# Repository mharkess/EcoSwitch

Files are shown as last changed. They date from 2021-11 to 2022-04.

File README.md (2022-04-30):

# <div id="top">EcoSwitch</div>
EcoSwitch is an automated, energy-saving system for brownstone fan coil units (FCUs). It provides a BU-specific solution for maintaining comfortable dorm temperatures. Our product is simple, cost-effective, and meets the needs of BU's students and employees alike.

## Table of Contents
  <ol>
    <li>
      <a href="#engineering-addendum">Engineering Addendum</a>
      <ul>
        <li><a href="#hardware">Hardware</a></li>
        <li><a href="#software">Software</a></li>
      </ul>
    </li>
    <li>
      <a href="#software-reports">Software Reports</a>
    </li>
    <li>
      <a href="#hardware-report">Hardware Report</a>
    </li>
    <li>
      <a href="#previous-reports">Previous Reports</a>
    </li>
    <li>
      <a href="#contact-us">Contact Us</a>
    </li>
  </ol>

## Engineering Addendum

### Hardware

#### Circuit
<p align="justify">All relevant details about the connection of the circuit and its components is described in the <a href="https://github.com/mharkess/EcoSwitch/blob/main/EcoSwitch_Circuit/circuit_README.md">circuit_README </a>. It lists all the electronics specifications and steps to construct the circuit from scratch. Also, the reasons for selecting the electronics are listed there.</p>

<p align="justify">The next steps for the circuit are:</p>
- Add a LCD screen to display the temperature reading of the sensor

<p align="justify">
  
#### Attachment
<p align="justify">All relevant details about the attachment is mentioned in the <a href="https://github.com/mharkess/EcoSwitch/blob/main/EcoSwitch_attachmen/README_Hardware_Attachment.md">attachment README</a>. All the desinging concepts 3D models are listed there.</p>

<p align="justify">It is important to note that inserting a thin rubber strip in between the dial and the attachment allows the attachment to fit tighter on the switch.</p>

#### Installation and casing
<p align="justify">
  All relevant description for the device casing and installation is described in the <a href="https://github.com/mharkess/EcoSwitch/blob/main/EcoSwitch_Casing_and_install/README_Hardware_Installation.md">installation README</a>. It contains 3D models for the casing and instructions for installation.
</p>

### Software

#### Database and Server
<p align="justify">
  All relevant details about the EC2 server and MySQL database is described in the <a href="https://github.com/mharkess/EcoSwitch/blob/main/EcoSwitch_Database/README_Software_Backend.md">backend README</a>. Everything that is needed to create instances in AWS and populate those instances with the necessary files is documented there. 
</p>

The next steps for the server and the database are:
  - Add another column could be added to the database to keep track of previous temperatures and humidities to be displayed for administrators. 
  - Add error checking for API requests (for wrong data types)
  - Make SQL queries from the API to the database more secure (ex. checking the query before submitting to the database)

 <p align="justify">
  As a note, some of the PHP API calls have trouble working, even when they are set up correctly. This happens namely to tha API calls that take in arguments from the packet body and are adding/subracting rows in the database. The only work around that seemed to resolve it was to redirect the call through a API service (like AWS API Gateway), so that the request first goes to the API service, then the server (the response goes from the server to the API service).
 </p>
 
  #### EcoSwitch Device
<p align="justify">
  All relevant details about the EcoSwitch Device are described in the 
  <a href="https://github.com/mharkess/EcoSwitch/blob/main/ESP32%20Code/README_Software_ESP32.md">ESP32 README</a>. 
  Everything needed to upload the project and run it is documented in there. 
</p>

The next steps for the EcoSwitch Device are:
  - Polish UI interface for users
  - Add extra items to Administration page (Like locking device locally)

 <p align="justify">
  As a note, if the device is unable to connect to the network when it first boots, the device will reset itself on every attempt. If internet connection is lost during normal operation, then the device will continue operating normally with the exception of uploading sensor data to the database and retrieving the user's target temperature from the databae.
 </p>

#### Mobile Application
<p align="justify">
  To begin development, please follow the instructions outlined in the 
  <a href="https://github.com/mharkess/EcoSwitch/blob/main/EcoSwitchApp/README_Software_MobileApp.md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">mobile application README</a>. 
  Everything needed to initially build the project and run it is documented there. Note that some of the tools used for development were not the latest version (i.e. Expo) and updating to the latest version may cause problems with running the application.
</p>

#### Website
<p align="justify">
  All relevant details on the website's current status can be found in its corresponding <a href="https://github.com/mharkess/EcoSwitch/blob/main/EcoSwitch%20Website/README_Software_Website.md">website README</a>.
</p>

Next steps for the website:
- Authentication checking to ensure the user is logged in before being able to access the dashboard and its other linked pages
- An interactive graph that plots the average temperatures and humidity levels for each location
- Error checking for the various inputs that are allowed
  - location-related inputs: ensure the building is a valid BU brownstone location
  - room number-related inputs: ensure the room exists in the specified location
  - student email-related inputs: ensure the student email exists and is from BU
  - device registration: ensure the device does not already exist in the database
  - location locking: ensure the location is not already locked
  - location unlocking: ensure the location is not already unlocked
  - student assignment: ensure the student has not already been assigned to the specified device
  - student removal: ensure the student has not already been removed from the specified device or has never been assigned to it
- Confirmation messages for form submissions

<p align="justify">It is worth keeping in mind that the React JS version the website has been built with is newer and therefore, older articles online that provide React JS tutorials may no longer be applicable. For example, the useHistory function has been replaced with useNavigate. Additionally, for forms, it is important to prevent the page from refreshing before the API call has been completed. Using the preventDefault method achieves this. Finally, to view console outputs, use the Developer Tools Console rather than the terminal that is being used to run the server.</p>

<p align="right">(<a href="#top">back to top</a>)</p>

## Software Reports

- [Database and Server](https://github.com/mharkess/EcoSwitch/blob/main/EcoSwitch_Database/README_Software_Backend.md)
- [EcoSwitch Device](https://github.com/mharkess/EcoSwitch/blob/main/EcoSwitch_Database/README_Software_ESP32.md)
- [Mobile Application](https://github.com/mharkess/EcoSwitch/blob/main/EcoSwitchApp/README_Software_MobileApp.md)
- [Website](https://github.com/mharkess/EcoSwitch/blob/main/EcoSwitch%20Website/README_Software_Website.md)

<p align="right">(<a href="#top">back to top</a>)</p>

## Hardware Report

- [Circuit](https://github.com/mharkess/EcoSwitch/blob/main/EcoSwitch_Circuit/circuit_README.md)
- [Attachment](https://github.com/mharkess/EcoSwitch/blob/main/EcoSwitch_attachmen/README_Hardware_Attachment.md)
- [Installation and Casing](https://github.com/mharkess/EcoSwitch/blob/main/EcoSwitch_Casing_and_install/README_Hardware_Installation.md)

<p align="right">(<a href="#top">back to top</a>)</p>

## Previous Reports

- [First Semester PDRR](https://github.com/mharkess/EcoSwitch/blob/main/Project%20Reports/First%20Semester%20PDRR%20Report.pdf)
- [User Manual](https://github.com/mharkess/EcoSwitch/blob/main/Project%20Reports/User%20Manual.pdf)
- First Prototype Testing:
  - [Test Plan](https://github.com/mharkess/EcoSwitch/blob/main/Project%20Reports/Testing/First%20Prototype%20Test%20Plan.pdf)
  - [Test Report](https://github.com/mharkess/EcoSwitch/blob/main/Project%20Reports/Testing/First%20Prototype%20Test%20Report.pdf)
- Second Prototype Testing:
  - [Test Plan](https://github.com/mharkess/EcoSwitch/blob/main/Project%20Reports/Testing/Second%20Prototype%20Test%20Plan.pdf)
  - [Test Report](https://github.com/mharkess/EcoSwitch/blob/main/Project%20Reports/Testing/Second%20Prototype%20Test%20Report.pdf)
- Final Prototype Testing:
  - [Test Plan](https://github.com/mharkess/EcoSwitch/blob/main/Project%20Reports/Testing/Final%20Prototype%20Test%20Plan.pdf)
  - [Test Report](https://github.com/mharkess/EcoSwitch/blob/main/Project%20Reports/Testing/Final%20Prototype%20Test%20Report.pdf)

<p align="right">(<a href="#top">back to top</a>)</p>

## Contact Us

If there are any further questions about this project, please contact the lead developers via email.
- mharkess@bu.edu
- kevend@bu.edu
- liaophie@bu.edu
- samcu@bu.edu
- thevenin@bu.edu 

<p align="right">(<a href="#top">back to top</a>)</p>

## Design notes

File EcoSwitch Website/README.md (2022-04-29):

# <div id="top">EcoSwitch Administrator Website</div>

## Table of Contents
  <ol>
    <li>
      <a href="#about-the-project">About The Project</a>
    </li>
    <li>
      <a href="#software-module-overview">Software Module Overview</a>
      <ul>
        <li><a href="#pages">Pages</a></li>
        <li><a href="#main-functionalities">Main Functionalities</a></li>
      </ul>
    </li>
    <li>
      <a href="#dependencies-between-modules">Dependencies Between Modules</a>
    </li>
    <li>
      <a href="#development-and-build-information">Development and Build Information</a>
    </li>
    <li>
      <a href="#getting-started">Getting Started</a>
      <ul>
        <li><a href="#prerequisites-installation">Prerequisites Installation</a></li>
        <li><a href="#usage">Usage</a></li>
      </ul>
    </li>
  <li>
      <a href="#contact">Contact</a>
    </li>
  </ol>

## About The Project
<p align="justify">
  The EcoSwitch website was designed to provide housing administrators and faculty with a way to register and install new devices, as well as monitor and control currently existing ones. The original problem statement required the EcoSwitch system to be tamper-proof, so the administration website was conceptualized and developed to meet that feature.
</p>

<p align="right">(<a href="#top">back to top</a>)</p>

## Software Module Overview
<p align="justify">There are several pages that currently make up the EcoSwitch website. While some of them are simple in their functions and exist to provide information about the website and overall system, others have more significant purposes and provide access to the main features that are described in detail below.</p>

### Pages
<p align="justify">All of these pages take the form of JS functions or components that are imported and linked together in the App.js file located in the src folder of this directory.</p>

#### Home, ComponentReplace, StudentApp, and ErrorPage
<p align="justify">The home page provides an overview of our system and gives users an easy way to access the rest of the website's components, including the device registration form and housing portal sign in page.</p>
  
<p align="justify">ComponentReplace and StudentApp do not currently contain interactive content; however, they are placeholders that have been created to give users a more thorough understanding of the other features we have designed our product to contain. For example, we planned to allow the device's attachment to be swappable in case it somehow became damaged. This allows facility workers to simply replace the attachment rather than the entire device, making it a cost-effective solution. Additionally, while the mobile app is not currently available through any app store, it is an important part of our deliverables and should be accessible to our users with any future usage of our system. Finally, the error page provides users with a readable error message in case they try to access a page that does not exist. These last three pages will not be shown below due to their lack of content.</p>

<div align="center">
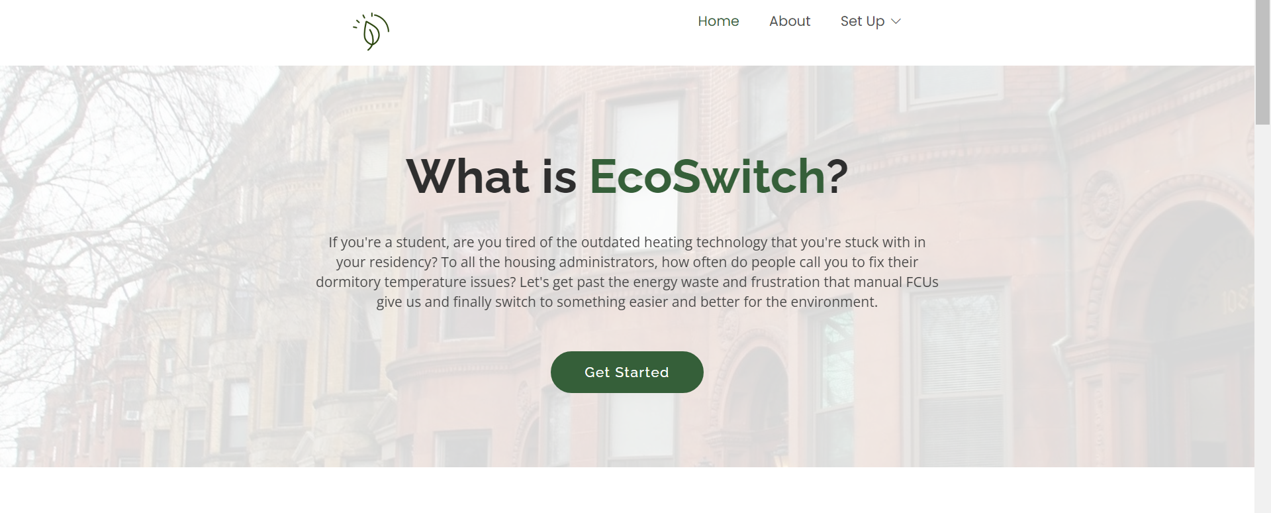
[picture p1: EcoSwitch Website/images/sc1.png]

</div>
<div align="center">
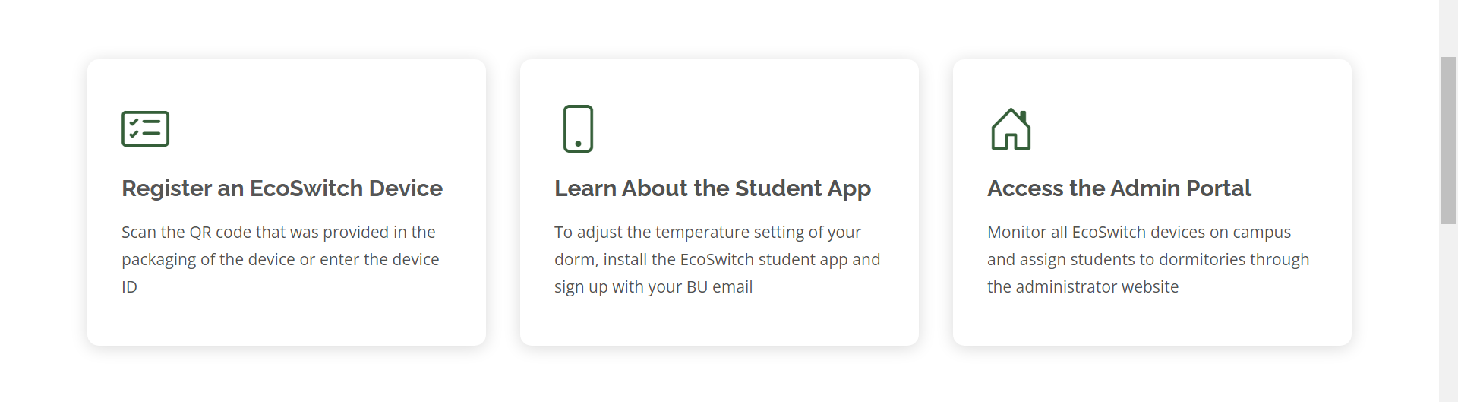
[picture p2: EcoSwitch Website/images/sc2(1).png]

</div>
<div align="center">
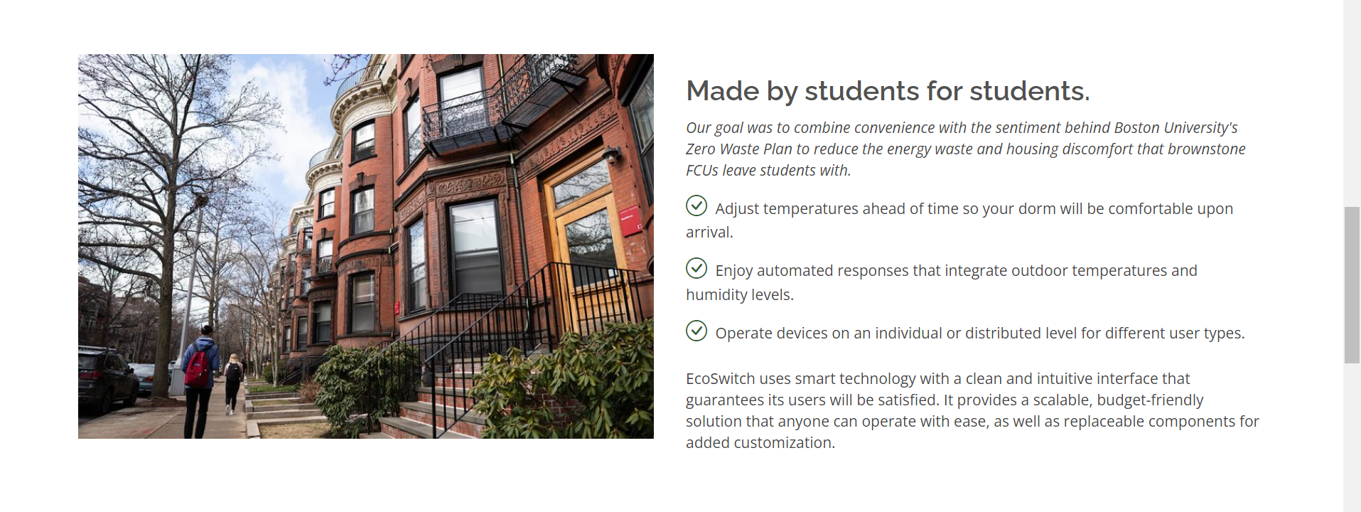
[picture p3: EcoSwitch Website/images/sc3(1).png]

</div>
<div align="center">
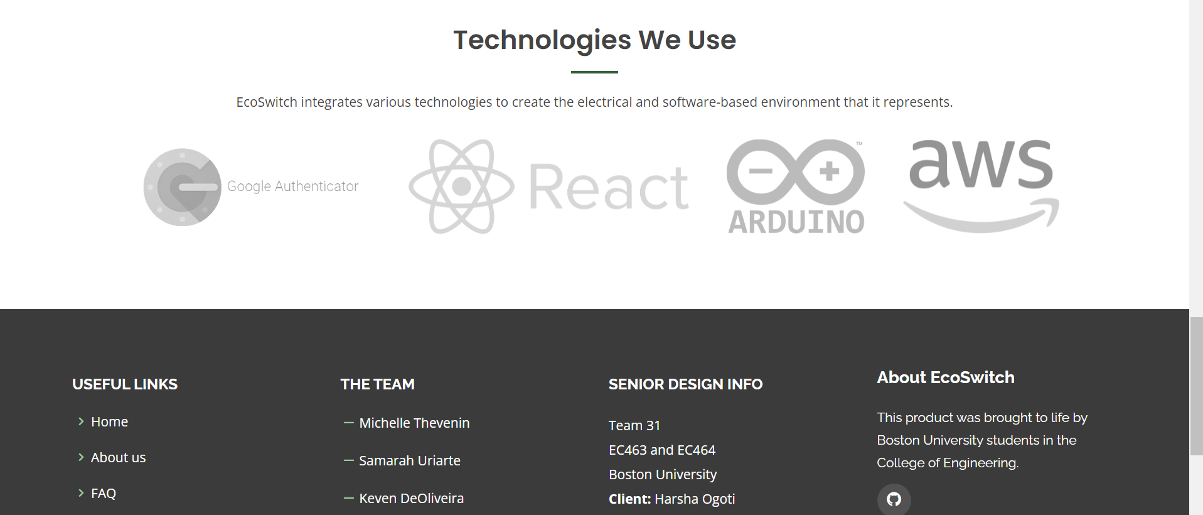
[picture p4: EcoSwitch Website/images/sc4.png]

</div>

#### Register
<p align="justify">This page is directly accessible from the website's home page and does not require users to be logged in for usage. It is important to the system's initial installation, as it allows individuals to register new EcoSwitch devices. It consists of a simple form that requests for the user to input the device ID, installation building location, installation room number. Additionally, we have designed a QR code that links to this page and would be placed within the device's packaging so users can easily scan it to set it up.</p>

<div align="center">
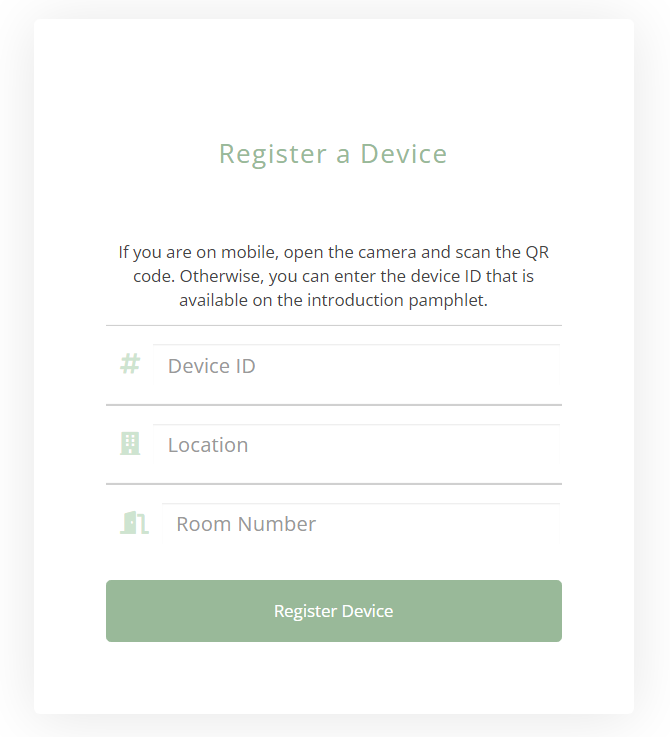
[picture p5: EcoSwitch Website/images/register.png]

</div>
</br>
<div align="center">
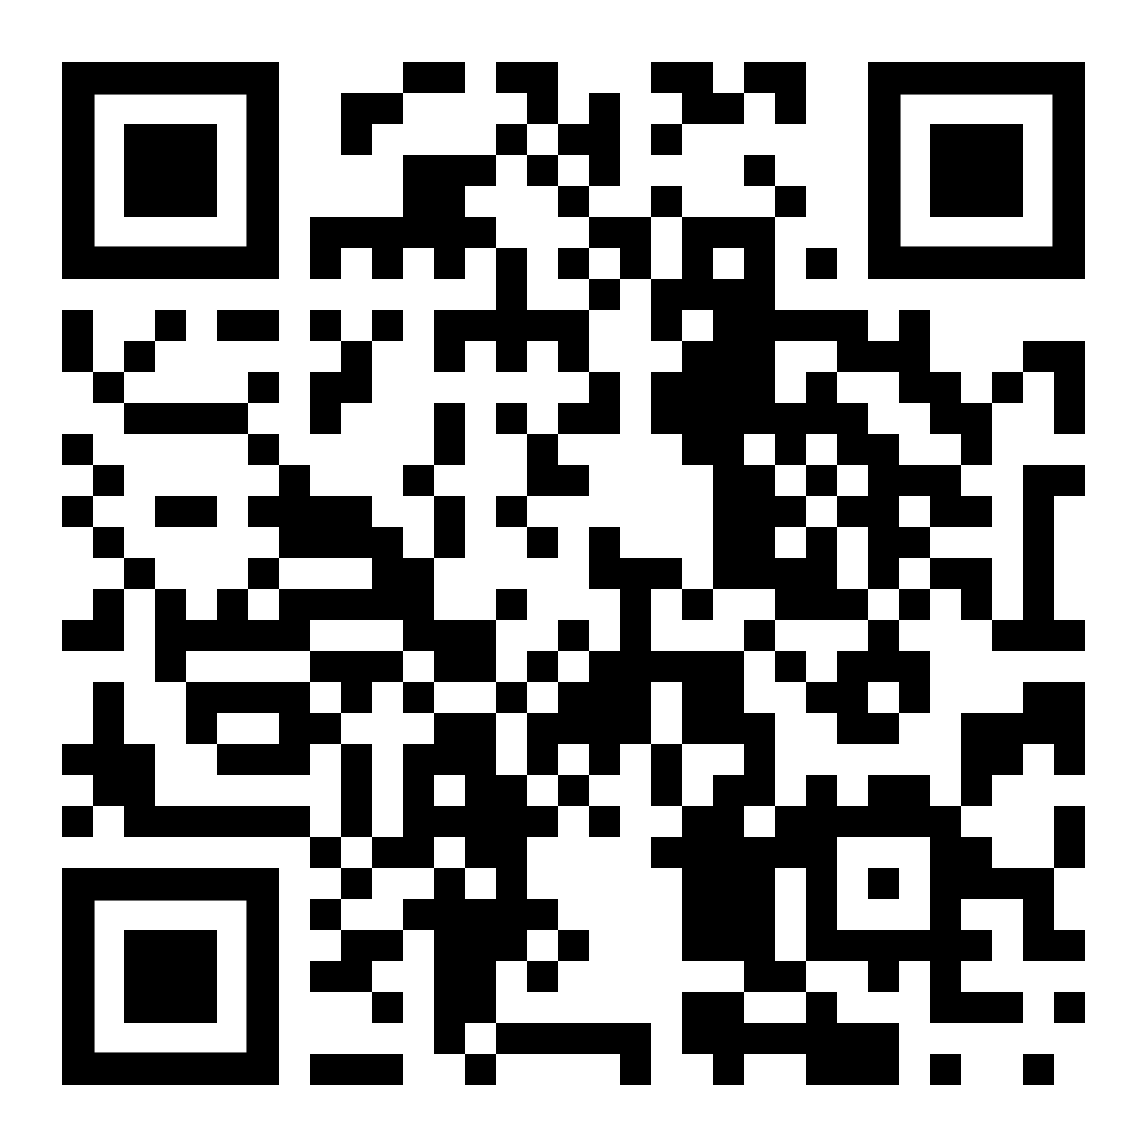
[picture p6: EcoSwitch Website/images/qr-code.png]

</div>

#### SignUp and SignIn
<p align="justify">These pages allow administrators to create an account and use it to sign in. They can also use Google as a provider and sign in with their Google account. This feature has been implemented with the JavaScript Firebase library and connects the application to a Firebase project that logs all user activity.</p>

<div align="center">
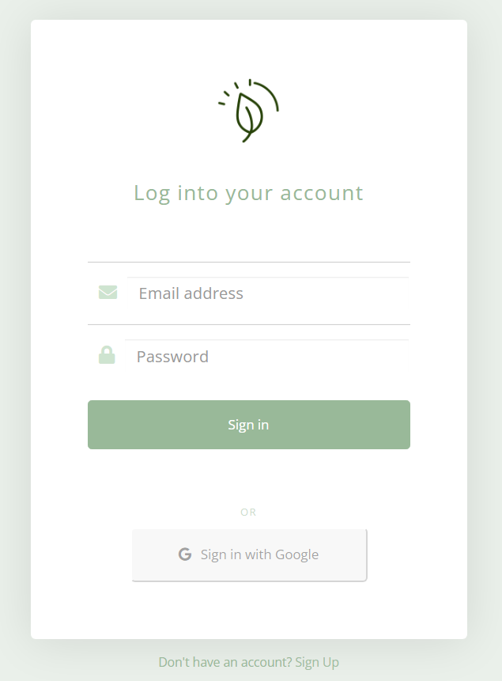
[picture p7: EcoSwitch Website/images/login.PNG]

</div>
</br>
<div align="center">
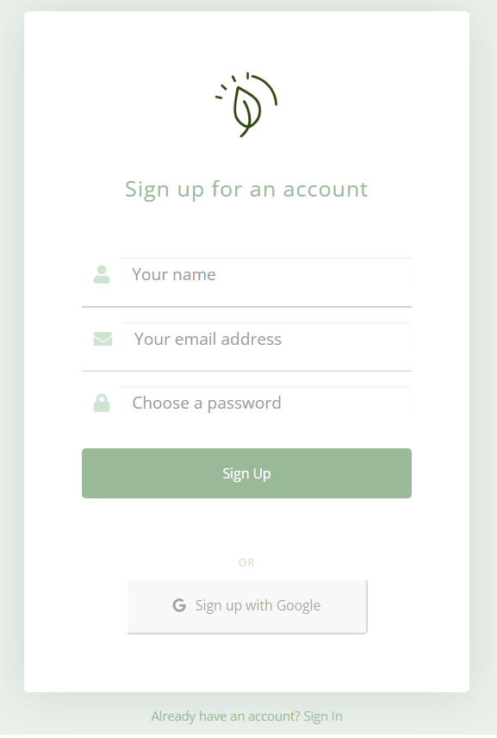
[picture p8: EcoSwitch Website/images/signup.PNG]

</div>

#### Main, DeviceAdjust, StudentAdd, and Profile
<p align="justify">The dashboard contains all the information for every EcoSwitch device that currently exists in the database. It is shown in a dynamic table that is bound to the database's entries. The empty space below was meant to hold a graph that provides a visual for the temperature and humidity levels for each building; however, this was not implemented due to a lack of time.</p>

<p align="justify">In addition to this page, there are the DeviceAdjust and StudentAdd pages that can be accessed through the sidebar. Both pages have a similar format that presents two tabs for the user to click on. Each tab brings up a separate form that does the opposite action of the other tab. For the DeviceAdjust page, there is a lock and unlock tab that allows admin to either prevent student input for a certain location and shut down all its FCUs or unlock the location and provide students with access to the devices in it again. For the StudentAdd page, one tab provides a form for registering students to a specific EcoSwitch device and the other provides a form for removing a student from a device's user list.</p>

<p align="justify">Finally, the profile page is another placeholder that has been designed to eventually display user information, such as one's name and email. Since this page does not contain any content, it has been emitted from the image set below.</p>

<div align="center">
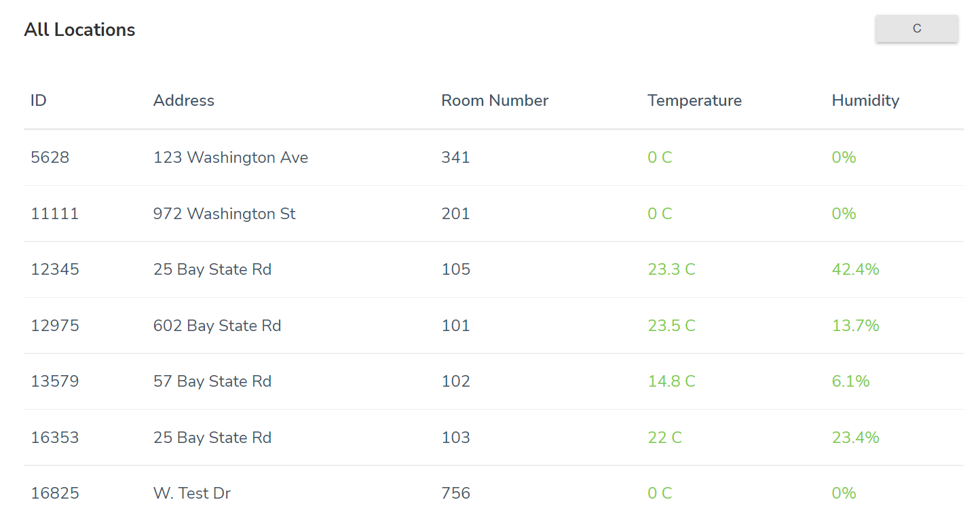
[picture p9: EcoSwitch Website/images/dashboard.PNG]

</div>
<div align="center">
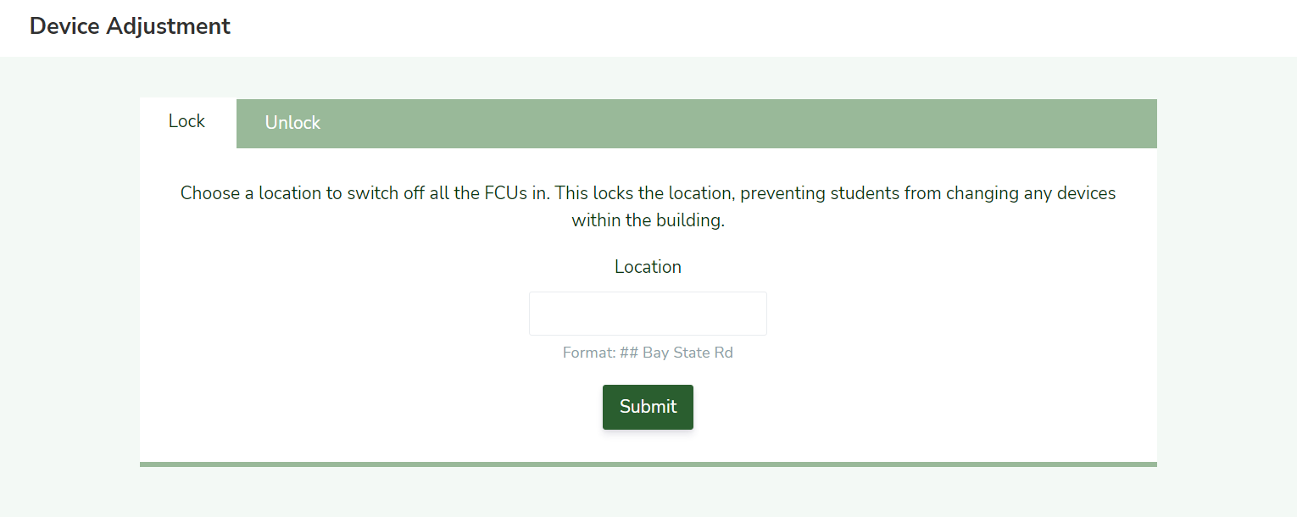
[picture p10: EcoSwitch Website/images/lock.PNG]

</div>
<div align="center">
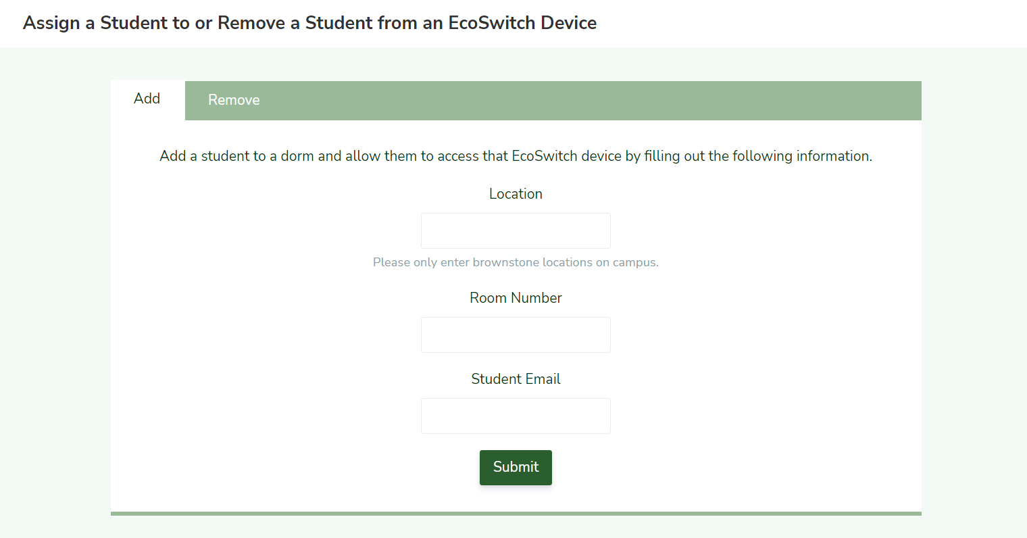
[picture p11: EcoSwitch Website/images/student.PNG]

</div>

### Main Functionalities
<p align="justify">A high-level description of all the website's main features are provided in this section, respective to the list of pages provided in the "Pages" section.</p>

#### Clean and Easy to Navigate Interface
<p align="justify">The UI and UX of the website's main pages have been designed to be user-friendly and provide content that helps them easily find their way around. The colors have also been chosen to reflect EcoSwitch's logo and general aesthetic. This is immediately evident upon the arrival of the home page, as it provides a navigation bar and large buttons that redirect users to the sign in page and device registration form.</p>

#### Device Registration
<p align="justify">As mentioned in the "Register" section, the EcoSwitch website offers the ability for users to register new EcoSwitch devices. This effectively adds them to the database and allows them to start communicating with the rest of the system. It is meant to be accessible and easy to use so the facility workers who would be setting up the devices in the dormitories would be able to do so without any difficulties. At the moment, the submission form does not have any error checking that guarantees the location and EcoSwitch ID is valid; however, this would be necessary to establish before product deployment.</p>

#### Account Creation
<p align="justify">Users are able to create an account with their email and a chosen password or through Google sign in. Upon a successful sign in request, they will be redirected to the dashboard page and their activity will be documented in the corresponding Firebase project. Currently, any individual can achieve this, though we would like there to be greater restrictions to those who can view all the EcoSwitch data and interact with the devices. However, we are unable to use Kerberos due to the security risks that would introduce. As a result, the dashboard does not require user authenitcation and the login feature has been implemented for concept development with the integration of Firebase.</p>

#### Data Querying
<p align="justify">A significant capability of the website is to communicate with the back end and its various databases through API calls. This is achieved with the JavaScript fetch function with the endpoint being chosen based on whether a GET or POST request is being made and from which database the information is being queried. API calls are used to register new devices, assign and remove students to and from EcoSwitch devices, attain all the information stored by each device, and lock and unlock specified locations.</p>

<p align="right">(<a href="#top">back to top</a>)</p>

## Dependencies Between Modules

<p align="right">(<a href="#top">back to top</a>)</p>

## Development and Build Information
All installed dependencies for the project can be found within the [package.json](https://github.com/mharkess/EcoSwitch/blob/main/EcoSwitch%20Website/package.json) and [package-lock.json](https://github.com/mharkess/EcoSwitch/blob/main/EcoSwitch%20Website/package-lock.json) files located in this directory.

This project was developed and built using the following programs and versions:

- [NodeJS v14.17.6](https://nodejs.org/en/download/)
- NPM v8.6.0

<p align="right">(<a href="#top">back to top</a>)</p>

## Getting Started

### Prerequisites Installation

Install the software mentioned above in the [Development and Build Information](#development-and-build-information) section. This varies per system and operating system. Please refer to the respective websites for further installation information.

Once the repository is cloned, navigate to this directory (.../EcoSwitch/EcoSwitch Website) and run the following code to automatically build the project and install its dependencies:

```sh
npm install
```

### Usage

For development mode, npm can be used as well.
1. In the project directory, start the session with the following command:

```sh
npm start
```
&nbsp;&nbsp;&nbsp;&nbsp;&nbsp;&nbsp;&nbsp;This will start the development server and the project can be accessed through localhost port 3000 ([http://localhost:3000](http://localhost:3000)).

**OR**

1. Access the project's pre-production build, hosted using Amplify. 
    - [Deployed Version](https://main.d3enog0k6n6e1t.amplifyapp.com/)
    - Please note that popups may be blocked, so the best way to create an account and subsequently log in is by entering your email and choosing a password through the sign-up page.

<p align="right">(<a href="#top">back to top</a>)</p>

## Contact

If there are any further questions about the application project, please contact the lead developer via email.
- samcu@bu.edu
- samarah.cu@gmail.com

<p align="right">(<a href="#top">back to top</a>)</p>

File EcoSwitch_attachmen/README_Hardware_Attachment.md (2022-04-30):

# EcoSwitch Attachment

## About the Attachemnt
  The Ecoswitch attachemnt is specifically designed to fit on top of an FCU switch located in a brownstone on Boston University’s campus. The attachment makes it possible to turn the dial using the motor. The hole at the top of the attachment is fit to the diameter of the motor shaft. Inserting rubber pieces allows for a tighter fit.</p>
Here is the 3D model:
smaller motor hole (2)
Here is the drawing:
[current attachment dimensions.pdf](https://github.com/mharkess/EcoSwitch/files/8595591/current.attachment.dimensions.pdf)

## Contact

If there are any further questions about this project, please contact the lead developer via email.
- thevenin@bu.edu 

<p align="right">(<a href="#top">back to top</a>)</p>

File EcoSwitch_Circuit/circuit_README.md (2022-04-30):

# EcoSwitch Circuit

## About the Circuit
The EcoSwitch circuit consists of an ESP32 microcontroller, a DTH22 temperature and humidity sensor, a L298N motor driver, a Nema 17 stepper motor, and a 12V battery pack with 8 AA alkaline batteries. It also includes a 5V regulator, a 10 kΩ resistor, an 100 nF ceramic capacitor, and a 1uF electrolytic capacitor.

The following is the circuit diagram:
current circuit diagram

The following is the hardware pinout of the ESP32 Pins for setup:
hardware pinout

Here is a sheet detailing our voltage measurements and power consumption:
[voltage measurement Project Team 31.xlsx](https://github.com/mharkess/EcoSwitch/files/8595606/voltage.measurement.Project.Team.31.xlsx)

Here is our Bill of Materials:
[Bill of Materials- EcoSwitch - Sheet1 (2).pdf](https://github.com/mharkess/EcoSwitch/files/8595609/Bill.of.Materials-.EcoSwitch.-.Sheet1.2.pdf)

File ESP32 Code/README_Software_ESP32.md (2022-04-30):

# EcoSwitch Device Software
## Table of Contents
  <ol>
    <li>
      <a href="#about-the-project">About The Project</a>
    </li>
    <li>
      <a href="#software-module-overview">Software Module Overview</a>
      <ul>
        <li><a href="#ecoswitch-temperature-algorithm">EcoSwitch Temperature Algorithm</a></li>
      </ul>
    </li>
    <li>
      <a href="#development-and-build-information">Development and Build Information</a>
    </li>
    <li>
      <a href="#getting-started">Getting Started</a>
      <ul>
        <li><a href="#upload-script">Upload Script</a></li>
        <li><a href="#device-setup">Device Setup</a></li>
      </ul>
    </li>
  <li>
      <a href="#contact">Contact</a>
    </li>
  </ol>

## About the Project
The EcoSwitch ESP32 code was designed to retrieve sensor data from the FCU and manage the temperature of the room via regulating the FCU temperature. This is done by running an algorithm to turn the FCU dial.  The original problem statement required the EcoSwitch device to detect temperature and humidity, and to be able to regulate the temperature based on that data. So, the ESP32 code was developed to meet that feature.

## Software Module Overview
Every aspect of the code of the ESP32 is stored on a single file. However the main part of the code that is used often is the Algorithm required to regulate the room temperature.
### EcoSwitch Temperature Algorithm
The algorithm takes the current temperature, a past temperature, the target temperature, a Boolean and the time since last running as inputs. 
The algorithm makes a slope based on the past temperature, current temperature and time. It will use this slope to calculate the predicted temperature.
Below is the formula that is used to predict the temperature:
<div align="center">

  </div>

With that predicted temperature, the algorithm will compare it to the target temperature after it compares the target temperature to the current temperature. Depending on the comparisons, the algorithm will either: increase the temperature setting by 1, decrease the temperature setting by 1 or keep the temperature setting the same.

## Dependencies Between Modules
Below is a flow chart depicting how the algorithm operates:
<div align="center">
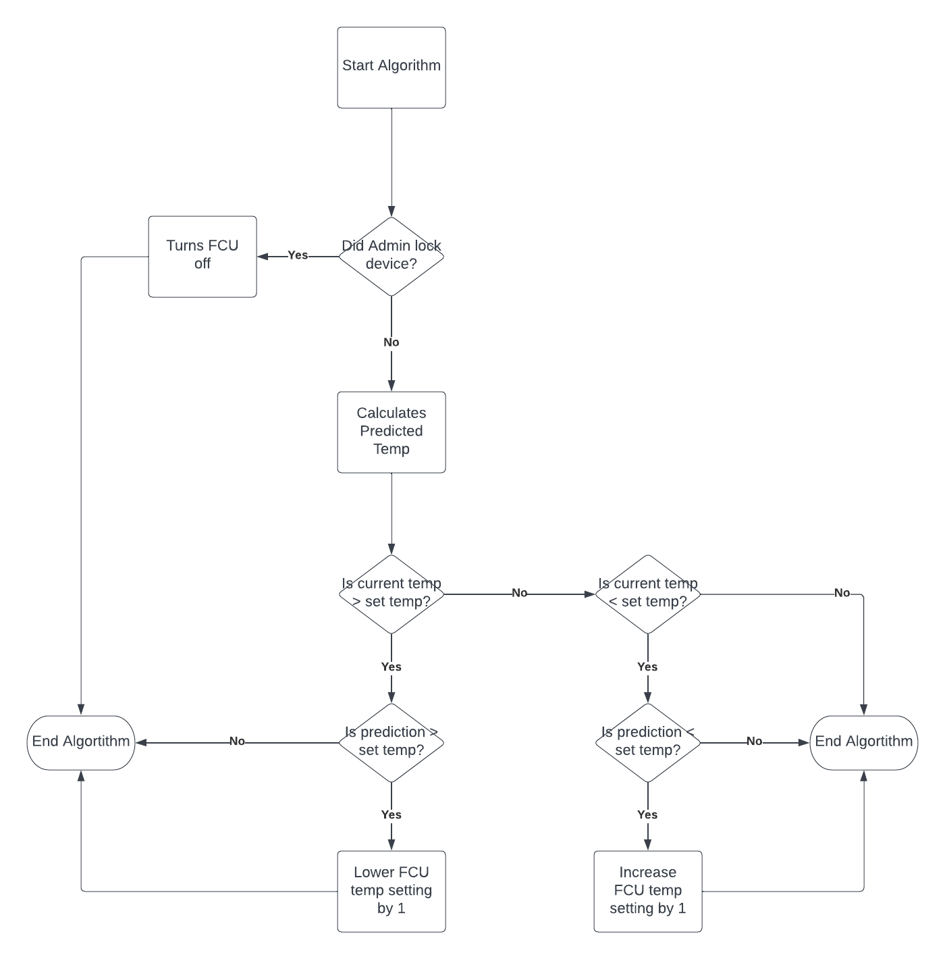
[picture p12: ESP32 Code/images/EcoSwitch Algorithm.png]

  </div>

## Development and Build Information
The program was developed with the following software:
* Arduino IDE v1.8.19

## Getting Started
### Prerequisites
You must install the ESP32 library in order to be able to program an ESP32 via Arduino IDE. Here is a tutorial that shows the exact process: [ESP32 Arduino IDE Tutorial](https://microcontrollerslab.com/install-esp32-arduino-ide/). You must also install the [AdaFruit DHT22 library](https://learn.adafruit.com/dht/using-a-dhtxx-sensor) to detect data from the DHT 22 sensor.

### Upload Script
Once the necessary libraries are installed, you can upload the ESP32 script that is provided in this repo. 
1. Navigate to `EcoSwitch/ESP32 Code/Ecoswitch_Dev/Ecoswitch_Dev.ino`. Double click on the file to open it up in Arduino IDE.
2. Once in Arduino IDE, connect the ESP32 to your computer.
3. After that upload the code to the ESP32 by clicking the "Upload" button.
<div align="center">
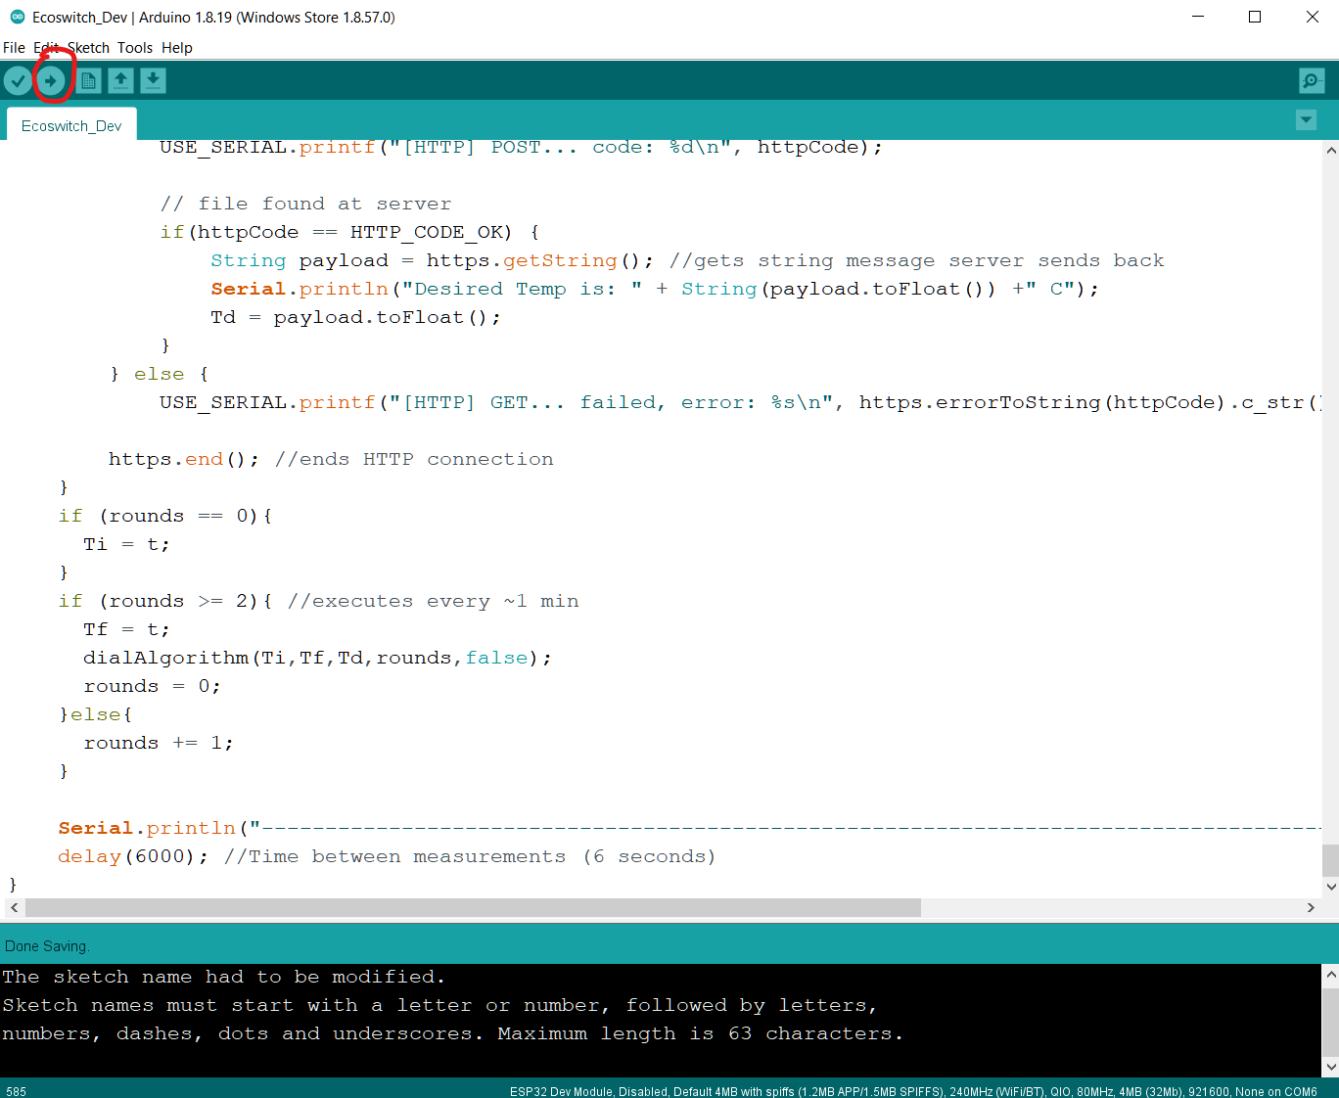
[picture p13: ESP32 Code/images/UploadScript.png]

  </div>

4. After the code has been uploaded, you can check if the code uploaded properly by opening the Serial Monitor to see if there is any output there.

### Device Setup
1. On the first boot, the device will want to know the WiFi credentials so that it can run. To do this, you must connect to the device via WiFi.
<div align="center">
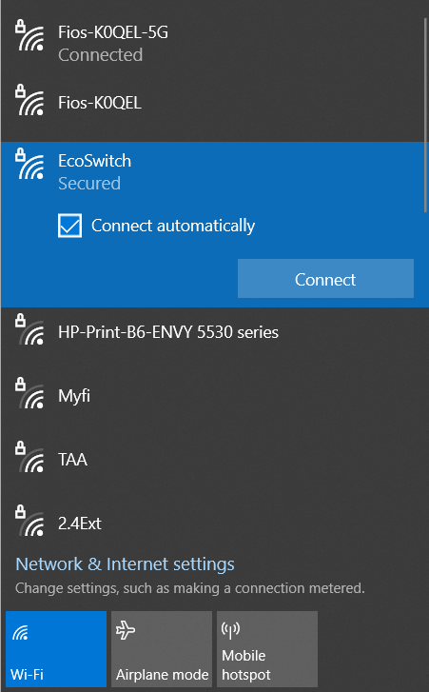
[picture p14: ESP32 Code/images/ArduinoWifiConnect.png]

  </div>

2. Once connected, navigate to `192.168.1.1` to access the HTML form to input the WiFi credentials.
<div align="center">
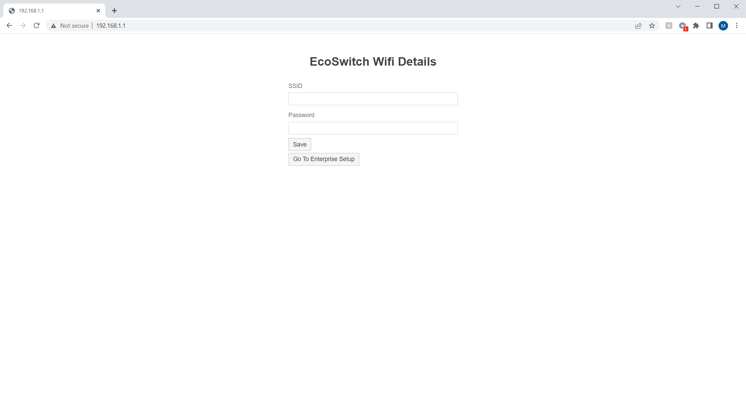
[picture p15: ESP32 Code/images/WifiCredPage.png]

  </div>

3. Once the credentials are written, click the submit button and look at the Serial Monitor to see if the device is connected to the internet.
4. If the device is connected to the internet, You will be able to see messages in the Serial Monitor regarding the Temperature, Humidity, and Current State of the device.
<div align="center">
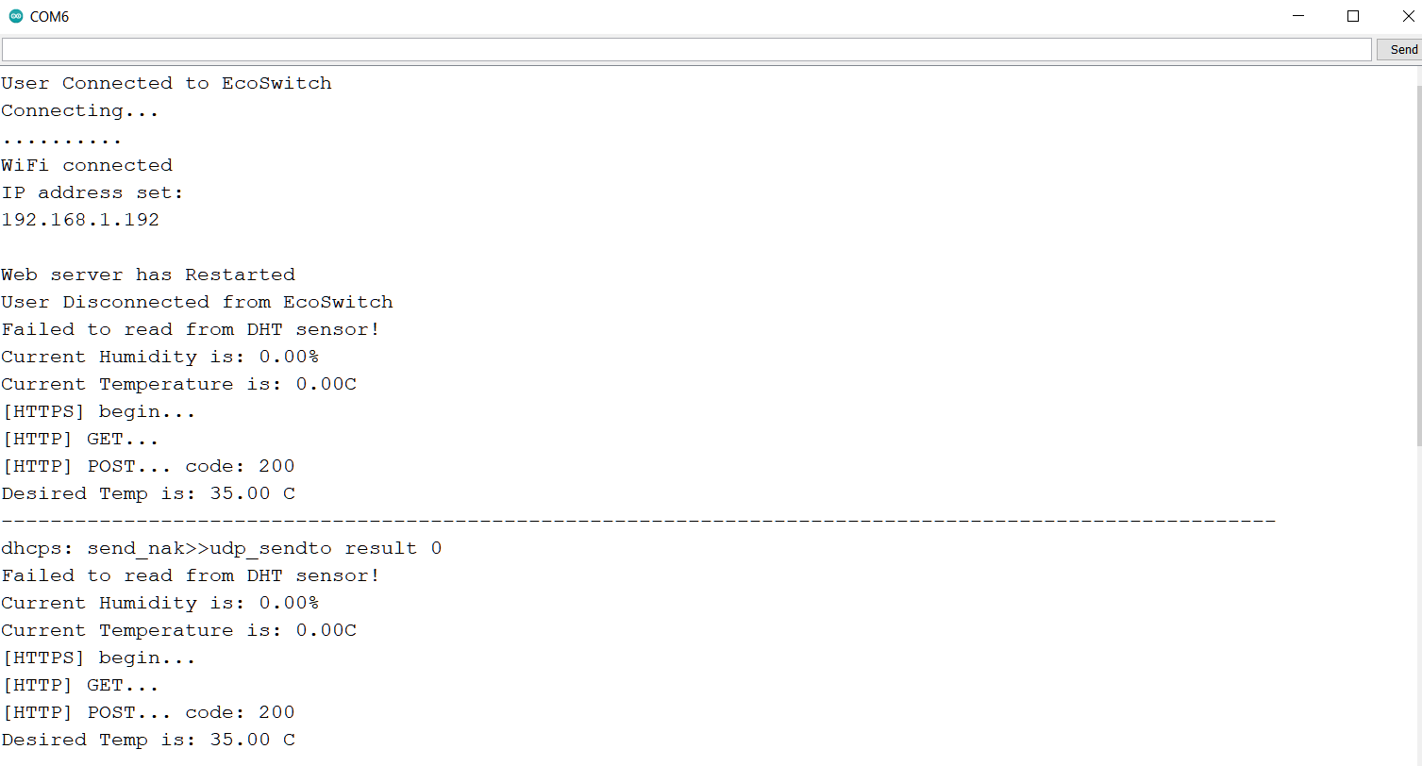
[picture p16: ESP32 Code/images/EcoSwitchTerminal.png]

  </div>

#### Potential Errors
If the device is having trouble connecting to a WiFi network, make sure that it is 2.4 GHz. If connection issues still persist after a few tries, you may want to connect to a different network (like a hotspot or an entirely different WiFi network).

## Contact
If there are any further questions about the application project, please contact the lead developer via email.
* mharkess@bu.edu

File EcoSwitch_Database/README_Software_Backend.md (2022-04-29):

# EcoSwitch Database and Server
## Table of Contents
  <ol>
    <li>
      <a href="#about-the-project">About The Project</a>
    </li>
    <li>
      <a href="#software-module-overview">Software Module Overview</a>
      <ul>
        <li><a href="#ecoswitch-api">EcoSwitch API</a></li>
      </ul>
    </li>
    <li>
      <a href="#development-and-build-information">Development and Build Information</a>
    </li>
    <li>
      <a href="#getting-started">Getting Started</a>
      <ul>
        <li><a href="#mariadb-setup-on-amazon-rds">MariaDB Setup on Amazon RDS</a></li>
        <li><a href="#apache-setup-on-amazon-ec2">Apache Setup on Amazon EC2</a></li>
        <li><a href="#amplify-hosting-setup">Amplify Hosting Setup</a></li>
      </ul>
    </li>
  <li>
      <a href="#contact">Contact</a>
    </li>
  </ol>

## About the Project
The EcoSwitch database and server was designed to store sensor data from the FCU and handle requests from users using the administrator website or the mobile application. The original problem statement required the EcoSwitch system to record temperature and humidity data, so the databases and server was developed to meet that feature.

## Software Module Overview
There are a handful of PHP files that act as the API for the EcoSwitch project. However, those files do not rely on each other in order to function. Each can be ran seperately and serve different purposes. Some update sensor data in the database and others add new records of devices to the database.

### Ecoswitch API
Below is a list of implemented API for EcoSwitch along with examples of valid calls, organized by the type of request being made. There is also a provided description of what each call is supposed to function as. Below, all of the example JSON's are assuming that you are using a JSON stringify function and a HTTP request library like fetch.  

All Requests will be received by the EC2 instance via its URL.  

So, to use the API, it would be in the format of: `URL/API`. From the API below, an example would be: `https://my-instance-public-dns-name/API/addUser.php?deviceId=<id>`

*Note: If HTTPS is giving issues when implementing the API endpoints, an alternative is using HTTP

#### GET Requests
##### /device_dataUpdate.php
  - Description: Updates temp and humidity of a particular device in the database (device is determined by their ID number)
  - Query Format:
    - `/device_dataUpdate.php?temperature=<temp>&humidity=<humidity>&deviceID=<id>` 
  - Example valid Query:
    - `https://my-instance-public-dns-name/API/device_dataUpdate.php?temperature=22.4&humidity=6.5&deviceID=12345`
##### /allUsers.php
  - Description: Retrieves table of all users in the database (table contains user's email, address and room number).
  - Query Format:
    - `/allUsers.php?deviceID=<id>`
  - Example of valid Query:
    - `https://my-instance-public-dns-name/API/allUsers.php?deviceID=12345`     
##### /allRecent.php
  - Description: Retrieves table of all devices in the database (table contains device ID, most recent temperature of their room and most recent humidity of their room).
  - Query Format:
    - `/allRecent.php?deviceID=<id>`
  - Example valid Query:
    - `https://my-instance-public-dns-name/API/allRecent?deviceID=12345`
##### /tempRequest.php
  - Description: Retrieves most recent temperature and humidity of a particular device from the database
  - Query Format:
    - `/tempRequest.php?DeviceID=<id>`
  - Example valid Query:
    - `https://my-instance-public-dns-name/API/tempRequest?DeviceID=12345` 
##### /getUser.php 
  - Description: Retrieves all information related to queried user (Email, Address, Room Number and DeviceID)
  - Query Format:
    - `/getUser.php?email=<email>`
  - Example valid Query:
    - `https://my-instance-public-dns-name/API/getUser?email=bob@bu.edu`
  - Return Value Format:
    - {"Student": "TEST@bu.edu", "Address": "101 Bay State Rd", "RoomNumber": "101", "DeviceID": "12345"}    

#### POST Requests
##### /addUser.php
  - Description: Adds users to a table relating users to the room and address that they are currently residing.
  - URL Query:
    -  `https://my-instance-public-dns-name/API/addUser`
  - Example valid JSON to send in body:
    - {"Email": "example@gmail.com", "Location": "123 Washington St", "RoomNumber": "1234"} 
##### /desiredTemp.php
  - Description: Changes the user's desired temperature of the room in the database
  - URL Query:
    -  `https://my-instance-public-dns-name/API/desiredTemp`
  - Example valid JSON to send in body:
    - {"DeviceID": "12345", "desiredTemp": "10"}
##### /changeState.php
  - Description: Locks all devices in a location to a setting of the admin's choosing
    - Note: States are defined as: -1,0,1,2,3. Any value greater than -1 will lock devices to a particular setting. State -1 allows state to be changed by student input. 
  - URL Query:
    -  `https://my-instance-public-dns-name/API/changeState.php`
  - Example valid JSON to send in body:
    - {"Location": "25 Bay State Rd", "State": "0"}
##### /removeUser.php
  - Description: Removes User from database, user will no longer to be able to control a device
  - URL Query:
    -  `https://my-instance-public-dns-name/API/removeUser.php`
  - Example valid JSON to send in body:
    - {"Location": "TEST", "Email": "TEST@bu.edu", "RoomNumber": "101"}
##### /addDevice.php
  - Description: Adds devices to a table relating devices to the room and address of the device's location.
  - URL Query:
    -  `https://my-instance-public-dns-name/API/addDevice.php`
  - Example valid JSON to send in body:
    - {"DeviceID": "46826", "Location": "972 Washington St", "RoomNumber": "10348"}  
## Dependencies Between Modules
This section provides a flowchart showing the generic movement of data from the client (via the mobile appplication or administrator website) to the database. Note that any API that is listed above can go into the second box as shown below.
<div align="center">
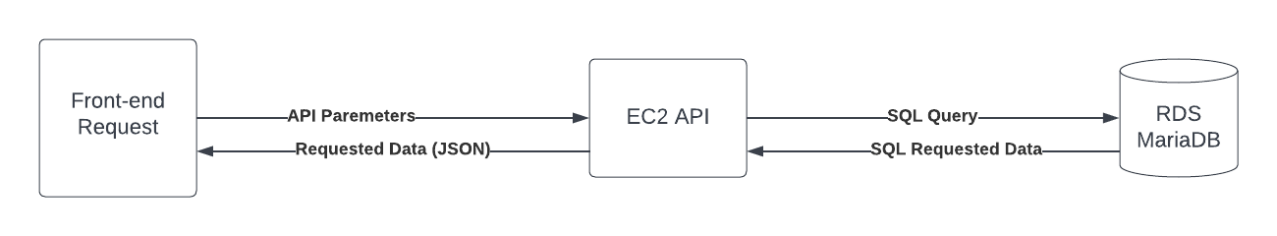
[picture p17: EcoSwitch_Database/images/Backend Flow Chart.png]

  </div>

## Development and Build Information
This project was built with the following programs, versions and hardware:
### RDS Build Information:
#### Software
* MariaDB v10.6.7
#### Hardware (Can be upgraded for better performance)
* 1 vCPU
* 1GiB RAM
* 20GiB SSD Storage
### EC2 Build Information:
#### Software
* Amazon Linux 2 Kernel v5.10 AMI 2.0.20220419.0 (with x86_64 Architecture)
* PHP v7.2
* Apache v2.4
#### Hardware (Can be upgraded for better performance)
* 1 vCPU
* 1GiB RAM
* 8 GiB SSD Storage

## Getting Started
### MariaDB Setup on Amazon RDS
1. In order to get started, you will need to have an Amazon AWS account. You can sign up for one here: [Amazon AWS](https://aws.amazon.com/free/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|PS-BI|Brand|Desktop|SU|AWS|Core|US|EN|Text&s_kwcid=AL!4422!10!71674567499740!71675011065633&s_kwcid=AL!4422!10!71674567499740!71675011065633&ef_id=d4773c0cc8251c3e64215e0735ed7a46:G:s&all-free-tier.sort-by=item.additionalFields.SortRank&all-free-tier.sort-order=asc&awsf.Free%20Tier%20Types=*all&awsf.Free%20Tier%20Categories=*all).

1. Once you have signed up for an account you will be greeted by the AWS dashboard. From here, you can follow the [RDS tutorial](https://docs.aws.amazon.com/AmazonRDS/latest/UserGuide/CHAP_GettingStarted.CreatingConnecting.MariaDB.html) to setup a MariaDB RDS instance in the AWS Documentation.

2. Once the RDS instance of the MySQL database has been created, there are two options to populate the database with schemas, tables and data. You can either SSH into the RDS instance from the command terminal or use a tool called MySQL Workbench. The continuation of the setup in this document will be using the MySQL Workbench as it provides a relatively good UI for displaying the data in the database, makes it easier to create/test SQL scripts and is a one-click connection to the cloud instance after first time setup.

The latest version of MySQL Workbench can be downloaded [here](https://dev.mysql.com/downloads/workbench/).

3. Once MySQL Workbench is opened, you can follow the [MySQL Workbench tutorial](https://dev.mysql.com/doc/workbench/en/wb-getting-started-tutorial-create-connection.html) provided by the official MySQL documentation to connect the Workbench to a remote SQL database (which in this case is the RDS instance).

4. Next, download the repo and navigate to `EcoSwitch/EcoSwitch_Database/RDS`. You will need the contents of this folder to populate the RDS instance with the appropriate schemas, tables and procedures.

5. Connect to the RDS instance via the Workbench and in the to menu, go to Edit -> Preferences -> Administration.

6. On this page, you will want to set the myssqldump.exe location to the mysqldump.exe file included in the repo (which is in `EcoSwitch/EcoSwitch_Database/RDS`).
<div align="center">
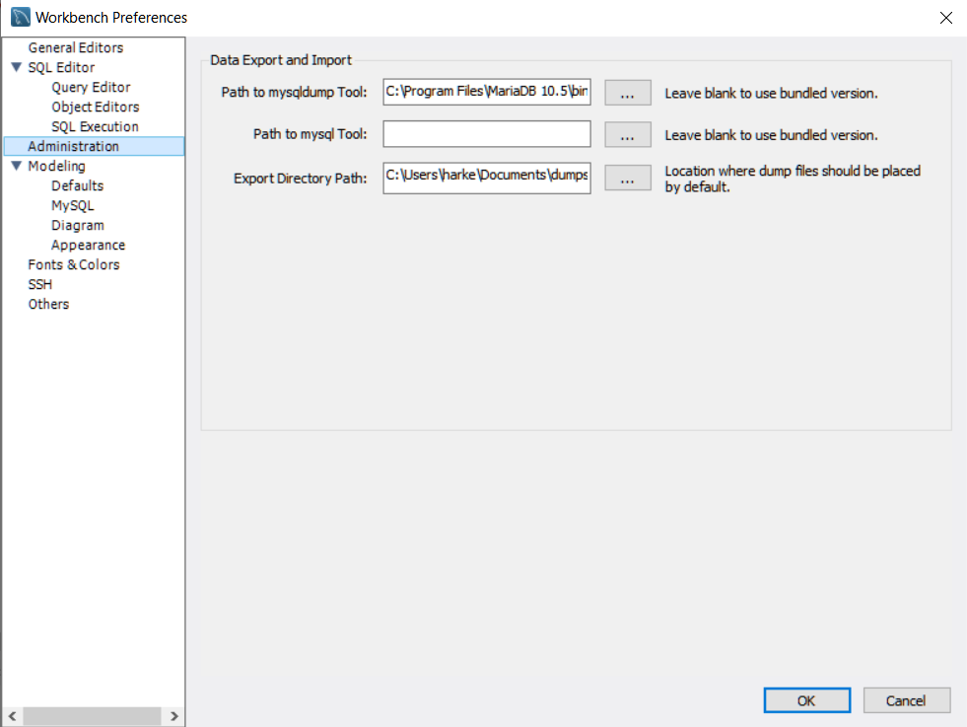
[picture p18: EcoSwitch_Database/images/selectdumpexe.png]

</div>

7. Once that is done, navigate to Server -> Data Import from the top menu. Select "Import from a Self-Contained File" and select the "EcoSwitchDB.sql" file in `EcoSwitch/EcoSwitch_Database/RDS`.
<div align="center">
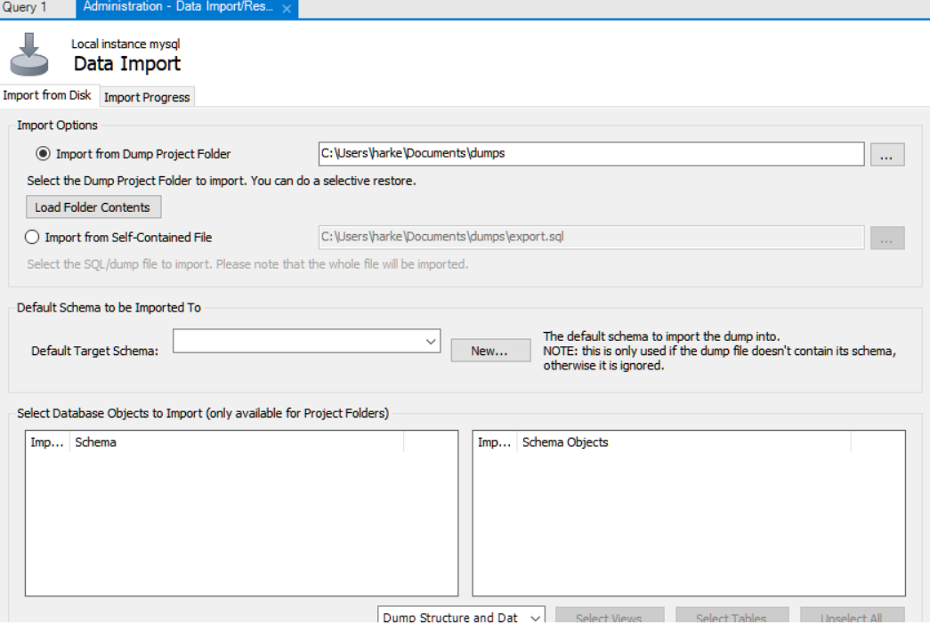
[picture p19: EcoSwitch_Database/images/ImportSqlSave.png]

</div>

8. Once the file is selected, click on the "Import Progress" tab and click the "Import" button. This should upload the schemas, test data, tables and procedures created for this project to the RDS Instance.
<div align="center">
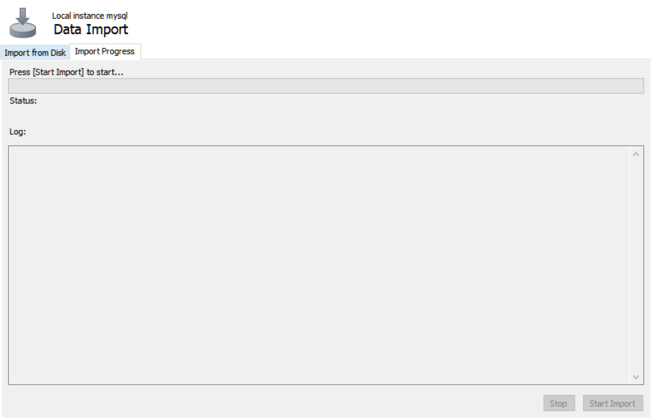
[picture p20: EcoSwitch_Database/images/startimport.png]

</div>

9. You can check the Workbench on the main page (the page that shows up after connecting to a DB) in the left side bar if all of the data is imported correctly. **NOTE:** To check the data on the left sidebar, you may need to refresh the sidebar by clicking the refresh icon at the top of the bar.
<div align="center">
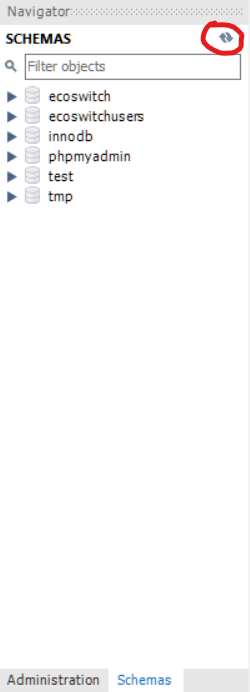
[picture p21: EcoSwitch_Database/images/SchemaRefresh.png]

</div>

### Apache Setup on Amazon EC2
To hold the API calls that this project uses, we store it on a EC2 instance running Apache to handle requests from the client.
1. Follow the setup to create an EC2 instance at this link: [EC2 Setup](https://docs.aws.amazon.com/AWSEC2/latest/UserGuide/EC2_GetStarted.html). When creating the instance, choose Amazon Linux 2 as the OS for the instance as this is the OS that this document refers to during the setup process.
2. After setting up the EC2 instance, to access the files in the instance, you will need to SSH into it. You will need at the Public IPv4 DNS to SSH, which can be found in the instances tab as well as the key-pair file created during setup (downloaded onto your machine). In order to do SSH in your terminal, you will need to run this command (you will need to replace the placeholders):
```sh
ssh -i /path/my-key-pair.pem my-instance-user-name@my-instance-public-dns-name
```

3. To configure Apache web server, PHP and MariaDB (in case you decide to not use RDS) you can follow the setup guide in this AWS documentation: [Apache Setup](https://docs.aws.amazon.com/AWSEC2/latest/UserGuide/ec2-lamp-amazon-linux-2.html).

4. To add the PHP files to the EC2 instance you can download the repository and copy the files to EC2. After the repository is downloaded you can run this command:
```sh
scp -i /path/my-key-pair.pem /path/my-php-folder ec2-user@my-instance-public-dns-name:/var/www/html
```
**NOTE:** Make sure you change the RDS URL to the URL of the instance that you have setup in the previous section for all of the PHP files before proceeding!

5. If successful, you can visit the PHP files in browser to see if they work (you can test with some of the GET API requests) with the following format: `https://my-instance-public-dns-name/API/api-call.php`

#### Potential Issues
If you are having trouble connecting to the EC2 instance, you can follow this [AWS documentation](https://docs.aws.amazon.com/AWSEC2/latest/UserGuide/AccessingInstancesLinux.html) about SSH connection to EC2.
 
### Amplify Hosting Setup
To host the admin website for this project, we decided to host it on Amplify as it could be deployed directly from the Github. To host the admin website on Amplify, navigate to the Amplify console and click on "Host Web App" in the dropdown bar in the top right of the page.
1. Click on the Github Icon on the page that loads and then you will be prompted to link your Github account to Amplify. NOTE: to deploy to Amplify in this manner, you MUST have ownership of the repo. 
2. Once your Github account is linked, you will be able to choose the repo to deploy to Amplify. Select the desired repo in the dropdown box. If you copied our repo, then you will only want to deploy a single folder in the repo. To do this, there is a selection at the bottom screen asking if you want to deploy a monorepo. Click the checkbox and then type in the path of the folder from the main file of the repo, which would be "EcoSwitch Website" (without quotations) if you are setting up the website.
3. Click next to bring you to a page showing the script that Amplify will use to compile and run the selected Web App. However, the default script must be changed to add extra libraries not included in `npm install`. Click on edit and replace the default script with the following:
```sh
version: 1
applications:
  - frontend:
      phases:
        preBuild:
          commands:
            - npm install
            - npm install firebase
            - npm install @firebase/analytics
            - npm install react-firebase-hooks
            - npm install react-chartjs-2 chart.js
        build:
          commands:
            - npm run build
      artifacts:
        baseDirectory: build
        files:
          - '**/*'
      cache:
        paths:
          - node_modules/**/*
    appRoot: EcoSwitch Website
``` 
4. After the script has been modified with the above, save it and continue clicking the next button until a "Save and Deploy" button appears. Make sure that the info that pops up on that page is correct. Once you have checked the information, click the "Save and Deploy" button and then wait between 5-8 minutes for Amplify to deploy the website.

5. Once the Web App has been deployed, Amplify will display a link to view the web app in the browser. From here you can test the website to see if it is being displayed properly and if the API calls are functioning.

#### Potential Errors
Some most of the errors that were encountered when deploying the website appeared during the build phase of the deployment. If you do get an error, you can click on the stage that failed during deployment to view the console logs. The most common errors were missing libraries (which can be added to the script above) or common coding mistakes as undeclared variables.  

## Contact
If there are any further questions about the application project, please contact the lead developer via email.
* mharkess@bu.edu

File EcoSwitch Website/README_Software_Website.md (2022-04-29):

# <div id="top">EcoSwitch Administrator Website</div>

## Table of Contents
  <ol>
    <li>
      <a href="#about-the-project">About The Project</a>
    </li>
    <li>
      <a href="#software-module-overview">Software Module Overview</a>
      <ul>
        <li><a href="#pages">Pages</a></li>
        <li><a href="#main-functionalities">Main Functionalities</a></li>
      </ul>
    </li>
    <li>
      <a href="#dependencies-between-modules">Dependencies Between Modules</a>
    </li>
    <li>
      <a href="#development-and-build-information">Development and Build Information</a>
    </li>
    <li>
      <a href="#getting-started">Getting Started</a>
      <ul>
        <li><a href="#prerequisites-installation">Prerequisites Installation</a></li>
        <li><a href="#usage">Usage</a></li>
      </ul>
    </li>
  <li>
      <a href="#contact">Contact</a>
    </li>
  </ol>

## About The Project
<p align="justify">
  The EcoSwitch website was designed to provide housing administrators and faculty with a way to register and install new devices, as well as monitor and control currently existing ones. The original problem statement required the EcoSwitch system to be tamper-proof, so the administration website was conceptualized and developed to meet that feature.
</p>

<p align="right">(<a href="#top">back to top</a>)</p>

## Software Module Overview
<p align="justify">There are several pages that currently make up the EcoSwitch website. While some of them are simple in their functions and exist to provide information about the website and overall system, others have more significant purposes and provide access to the main features that are described in detail below.</p>

### Pages
<p align="justify">All of these pages take the form of JS functions or components that are imported and linked together in the App.js file located in the src folder of this directory.</p>

#### Home, ComponentReplace, StudentApp, and ErrorPage
<p align="justify">The home page provides an overview of our system and gives users an easy way to access the rest of the website's components, including the device registration form and housing portal sign in page.</p>
  
<p align="justify">ComponentReplace and StudentApp do not currently contain interactive content; however, they are placeholders that have been created to give users a more thorough understanding of the other features we have designed our product to contain. For example, we planned to allow the device's attachment to be swappable in case it somehow became damaged. This allows facility workers to simply replace the attachment rather than the entire device, making it a cost-effective solution. Additionally, while the mobile app is not currently available through any app store, it is an important part of our deliverables and should be accessible to our users with any future usage of our system. Finally, the error page provides users with a readable error message in case they try to access a page that does not exist. These last three pages will not be shown below due to their lack of content.</p>

<div align="center">

</div>
<div align="center">

</div>
<div align="center">

</div>
<div align="center">

</div>

#### Register
<p align="justify">This page is directly accessible from the website's home page and does not require users to be logged in for usage. It is important to the system's initial installation, as it allows individuals to register new EcoSwitch devices. It consists of a simple form that requests for the user to input the device ID, installation building location, installation room number. Additionally, we have designed a QR code that links to this page and would be placed within the device's packaging so users can easily scan it to set it up.</p>

<div align="center">

</div>
</br>
<div align="center">

</div>

#### SignUp and SignIn
<p align="justify">These pages allow administrators to create an account and use it to sign in. They can also use Google as a provider and sign in with their Google account. This feature has been implemented with the JavaScript Firebase library and connects the application to a Firebase project that logs all user activity.</p>

<div align="center">

</div>
</br>
<div align="center">

</div>

#### Main, DeviceAdjust, StudentAdd, and Profile
<p align="justify">The dashboard contains all the information for every EcoSwitch device that currently exists in the database. It is shown in a dynamic table that is bound to the database's entries. The empty space below was meant to hold a graph that provides a visual for the temperature and humidity levels for each building; however, this was not implemented due to a lack of time.</p>

<p align="justify">In addition to this page, there are the DeviceAdjust and StudentAdd pages that can be accessed through the sidebar. Both pages have a similar format that presents two tabs for the user to click on. Each tab brings up a separate form that does the opposite action of the other tab. For the DeviceAdjust page, there is a lock and unlock tab that allows admin to either prevent student input for a certain location and shut down all its FCUs or unlock the location and provide students with access to the devices in it again. For the StudentAdd page, one tab provides a form for registering students to a specific EcoSwitch device and the other provides a form for removing a student from a device's user list.</p>

<p align="justify">Finally, the profile page is another placeholder that has been designed to eventually display user information, such as one's name and email. Since this page does not contain any content, it has been emitted from the image set below.</p>

<div align="center">

</div>
<div align="center">

</div>
<div align="center">

</div>

### Main Functionalities
<p align="justify">A high-level description of all the website's main features are provided in this section, respective to the list of pages provided in the "Pages" section.</p>

#### Clean and Easy to Navigate Interface
<p align="justify">The UI and UX of the website's main pages have been designed to be user-friendly and provide content that helps them easily find their way around. The colors have also been chosen to reflect EcoSwitch's logo and general aesthetic. This is immediately evident upon the arrival of the home page, as it provides a navigation bar and large buttons that redirect users to the sign in page and device registration form.</p>

#### Device Registration
<p align="justify">As mentioned in the "Register" section, the EcoSwitch website offers the ability for users to register new EcoSwitch devices. This effectively adds them to the database and allows them to start communicating with the rest of the system. It is meant to be accessible and easy to use so the facility workers who would be setting up the devices in the dormitories would be able to do so without any difficulties. At the moment, the submission form does not have any error checking that guarantees the location and EcoSwitch ID is valid; however, this would be necessary to establish before product deployment.</p>

#### Account Creation
<p align="justify">Users are able to create an account with their email and a chosen password or through Google sign in. Upon a successful sign in request, they will be redirected to the dashboard page and their activity will be documented in the corresponding Firebase project. Currently, any individual can achieve this, though we would like there to be greater restrictions to those who can view all the EcoSwitch data and interact with the devices. However, we are unable to use Kerberos due to the security risks that would introduce. As a result, the dashboard does not require user authenitcation and the login feature has been implemented for concept development with the integration of Firebase.</p>

#### Data Querying
<p align="justify">A significant capability of the website is to communicate with the back end and its various databases through API calls. This is achieved with the JavaScript fetch function with the endpoint being chosen based on whether a GET or POST request is being made and from which database the information is being queried. API calls are used to register new devices, assign and remove students to and from EcoSwitch devices, attain all the information stored by each device, and lock and unlock specified locations.</p>

<p align="right">(<a href="#top">back to top</a>)</p>

## Dependencies Between Modules
<p align="justify">This section provides a flowchart that illustrates all the dependencies and connections between the aforementioned software modules, as well as any relevant functions within them.</p>

<div align="center">
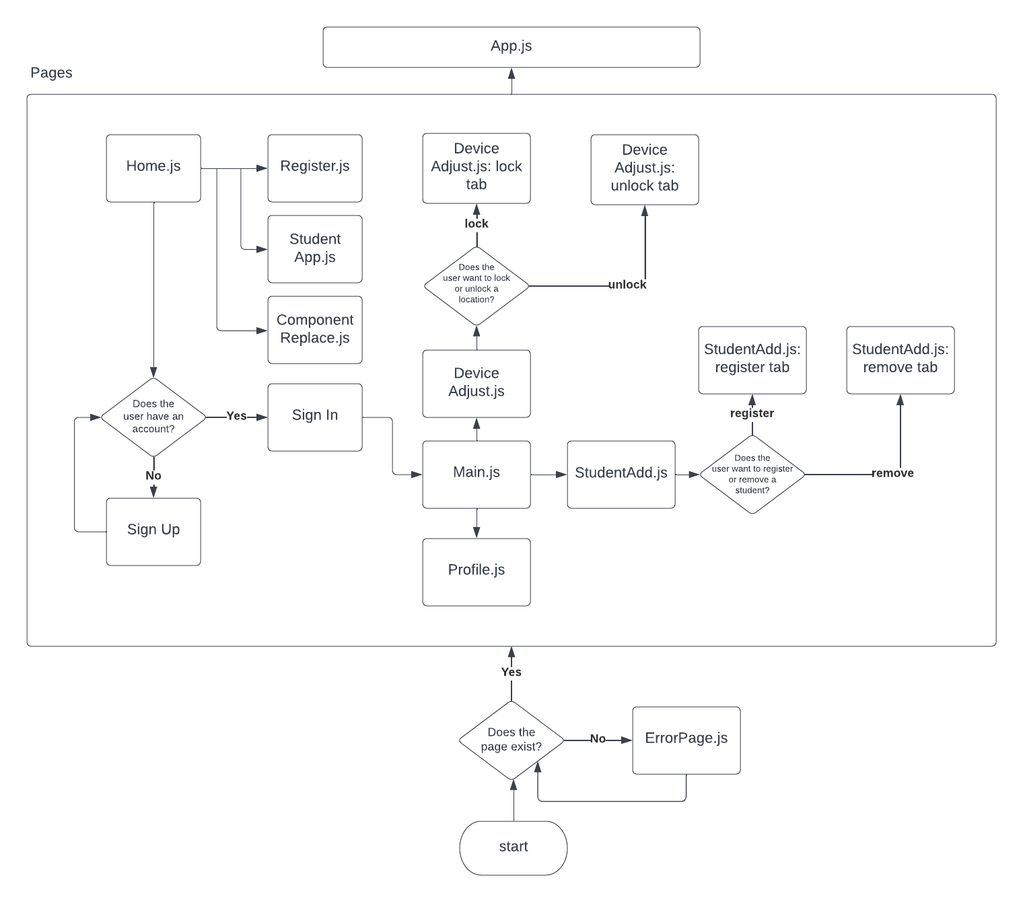
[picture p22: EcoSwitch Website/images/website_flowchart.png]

</div>

<p align="right">(<a href="#top">back to top</a>)</p>

## Development and Build Information
All installed dependencies for the project can be found within the [package.json](https://github.com/mharkess/EcoSwitch/blob/main/EcoSwitch%20Website/package.json) and [package-lock.json](https://github.com/mharkess/EcoSwitch/blob/main/EcoSwitch%20Website/package-lock.json) files located in this directory.

This project was developed and built using the following programs and versions:

- [NodeJS v14.17.6](https://nodejs.org/en/download/)
- NPM v8.6.0

<p align="right">(<a href="#top">back to top</a>)</p>

## Getting Started

### Prerequisites Installation

Install the software mentioned above in the [Development and Build Information](#development-and-build-information) section. This varies per system and operating system. Please refer to the respective websites for further installation information.

Once the repository is cloned, navigate to this directory (.../EcoSwitch/EcoSwitch Website) and run the following code to automatically build the project and install its dependencies:

```sh
npm install
```

### Usage

For development mode, npm can be used as well.
1. In the project directory, start the session with the following command:

```sh
npm start
```
&nbsp;&nbsp;&nbsp;&nbsp;&nbsp;&nbsp;&nbsp;This will start the development server and the project can be accessed through localhost port 3000 ([http://localhost:3000](http://localhost:3000)).

**OR**

1. Access the project's pre-production build, hosted using Amplify. 
    - [Deployed Version](https://main.d3enog0k6n6e1t.amplifyapp.com/)
    - Please note that popups may be blocked, so the best way to create an account and subsequently log in is by entering your email and choosing a password through the sign-up page.

<p align="right">(<a href="#top">back to top</a>)</p>

## Contact

If there are any further questions about the application project, please contact the lead developer via email.
- samcu@bu.edu
- samarah.cu@gmail.com

<p align="right">(<a href="#top">back to top</a>)</p>

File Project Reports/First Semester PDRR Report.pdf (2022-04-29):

EC463 - B OS TON UNIVER S ITY ELE C TR IC AL & COMPUTER ENGINE ER ING C AP S TONE SE NIOR DES IGN P ROJEC T

B oston University E lectrical & C omputer E ngineering C apstone S enior Design Project

# E coS witch – An Autonomous FC U Maintenance S ystem

J iawei Liao, Keven DeOliveira, Michelle Thevenin, S amarah Uriarte, and Michael Harkes s

Abstract —Manual FCUs in brownstones lead to uncomfortably warm rooms , causing occupants to either turn them off or open a window in an attempt to balance out the temperature. The former is inc onvenient and the latter results in a waste of energy. A cost -effective solution that offers multi -party accessibility is required to address this problem. To facilitate a more enjoyable housing experience and provide a centralized maintenance application to Boston University housing administrators, we propose EcoSwitch, an autonomous FCU dial mount with integrated applications which will allow both residents and managers to mon itor and adjust FCU temperatures. In addition, it will query local weather information to maintain accurate performance and store relevant information in a highly accessible database, which will allow FCU functionality to be evaluated. EcoSwitch has been o ptimized for the management of Boston University’s campus life and will establish applications with functions that are appropriate for both administrators and students.

Index Terms — Autonomous system, Design, Real-time and embedded systems , Energy efficiency and conservation

————————————————
- Jiawei Liao EE’ 22. E-mail: liaophie@bu.edu
- Keven DeOliveira CE’ 22. E-mail: kevend@bu.edu
- Michelle Thevenin EE’ 22. E-mail: thevenin@bu.edu
- Samarah Uriarte CE’ 22. E-mail: samcu@bu.edu
- Michael Harkess CE’ 22. E-mail: mharkess@bu.edu

———————— ◆ ————————

1 NEED FOR THIS PROJECT
Many brownstone apartments on Boston University’s campus still use FCUs for indoor heating in the winter. This process is not controlled by the occupants in any way. Once FCUs are turned on for the winter, they are often left on for the remainder of the season. This situation leads to an uncomfortably warm room. Occupants typically aim to solve this problem by shutting the FCU off altogether or opening a window to balance the temperature on the inside. Opening a window while an FCU is running is a direct waste of energy and valuable resources.
Building administrators want to monitor room temperatures on a weekly basis to ensure that the FCUs are working properly. At the same time, they want the FCUs to work more efficiently so that energy is not wasted. Brownstone residents want an easy way to control their room temperatures so that it stays within a desirable range. Both students and administrators want a solution that is specific to Boston University so that it is cost effective and optimized for dormitories.
Boston University has a zero waste plan that aims to eliminate all waste by 2030. The plan is to redesign systems, reuse resources, change the culture, and develop sustainable markets. With EcoSwitch, we aim to automate the FCU control system in an effort to be more conscious of Boston University’s sustainability goals. Our design supports BU’s plan by providing a solution to the waste of energy that occurs as a result of using FCUs.
EcoSwitch will address this issue by allowing students to adjust the temperature of their dormitories according to their liking. EcoSwitch will automatically adjust the FCU to the desired temperature. EcoSwitch will be designed for long-term use and will be friendly to the environment.

2 PROBLEM STATEMENT & DELIVERABLES
Our proposed system design consists of several key components that all contribute to the overall maintenance of brownstone dormitory temperature and humidity levels.

2.1 Problem Statement
By integrating autonomous technology with simple applications for customizable temperature monitoring and management, EcoSwitch solves the problems of students facing uncomfortable dorm conditions and administrators having difficulty in efficiently reducing FCU energy waste. With the goal of achieving zero waste by 2030 [1] and a more general desire to increase the quality of student life on campus, our solution has been optimized for Boston University staff and students to ensure both parties’ needs are being met.
The high-level solution that forms our system design is partitioned into two separate sets of user and application interfaces and a centralized server that will process the data received from each EcoSwitch device. This solution addresses the different functionalities students and administrators require. Options for reading in and displaying temperature and humidity levels, filtered between specific individual students’ residencies to all of Boston University’s brownstones, will be available and chosen depending on the interface. Both parties will be able to control dorm temperatures as well; however, administrators will have the

2 | EC463 - B OS TON UNIVE R S ITY ELEC TR IC AL & COMPUTER ENGINE ER ING C AP S TONE S ENIOR DES IGN
| P R OJEC T
ability to override student input to ensure energy waste is
minimized.
Both the website and mobile app clients will use sensor information and functions that control the EcoSwitch
device to achieve FCU automation and remote adjustment capabilities. To reduce computational redundancies and bandwidth requirements, the website and mobile app will connect to a single server that will have data streamed in and distributed to the appropriate user. After user responses reach the server, it will deliver back calculated temperatures after processing these inputs. Each EcoSwitch device that will be registered with a dormitory will connect to this same server; this architecture allows all EcoSwitch devices to be linked to a centralized hub for ease of data distribution. Furthermore, a database will be maintained that contains temperature and humidity levels, allowing administrators to access past information and assess FCU functionality. The EcoSwitch administrator website will also produce graphs that plot dorm conditions for up to 3 days. Local weather information will be queried for through an API and used to determine individual EcoSwitch device instructions, a feature that guarantees dorm temperatures that more accurately match user input.
The EcoSwitch device will be a compact, battery-powered apparatus that reads in temperature and humidity information and relays it to the centralized server. Comprising a temperature and humidity sensor, microcontroller, and rotary actuator, the simple and cost-effective circuit design fulfills low-cost specifications. Our hardware design also includes an inexpensive attachable component that will fasten to the actuator and can easily be swapped for a new attachment if it becomes damaged. The entire device will be subject to safety constraints which make it suitable for the environment near the FCU’s surface.
The EcoSwitch devices will be programmed to collect data every 5 minutes; thus, there is no network strain or reliance on consistent WiFi connection. Computations will be performed in the central server, iterating through each registered EcoSwitch device after taking input from either administrators or students. The calculations will depend on local weather information that will be received through an API and combined with sensor data, as well as any experiment-based observations that are developed on the relationship between FCU surface temperature and the individual dormitory conditions. The EcoSwitch devices will then receive the results of these computations and execute instructions that will turn the actuator accordingly, ensuring the desired temperatures in the dormitories are reached.
2.2 Deliverables
A safely mountable device capable of:
1. Processing data and outputting information through a microcontroller
2. Sensing temperature and humidity levels
3. Attaching to and spinning a swappable attachment that will turn radiator dial knob
4. Withstanding heat from attached/nearby radiator and avoid tampering
5. Consuming low energy from a rechargeable battery

A cross-platform application capable of:
1. Periodically reporting sensed temperature and humidity levels to user
2. Allowing user to set desired range for temperature

An administration website capable of:
1. Monitoring the status of all devices connected to the Boston University housing and network
2. Overriding signals to individual devices
3. Logging and storing temperature and humidity data

3 VISUALIZATION
In this section, we will describe the three main aspects of our system that can be meaningfully visualized.

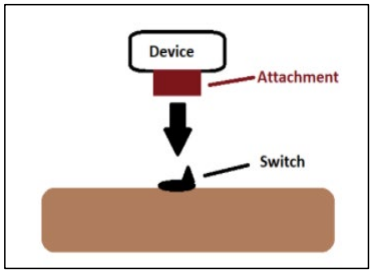
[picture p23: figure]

Fig. 1. This is a general depiction of the device in question. All the components, such as the microcontroller and sensors, will be housed in a small shell that will act as the “body” of the device. The attachment will be detachable and swappable for easy maintenance and replaceability.

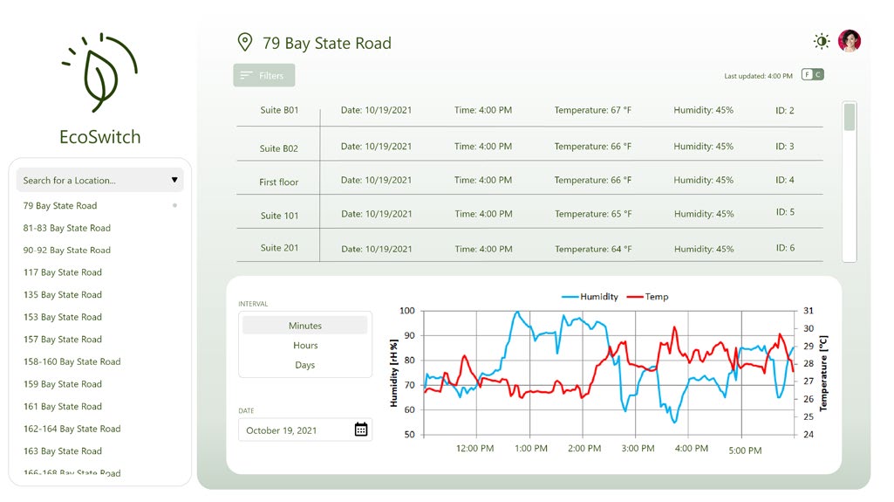
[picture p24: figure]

Fig. 2. A mockup of the administrator website UI. This website will allow admins to view past and current temperatures across every room. It will also provide the ability to override student input in dorms as needed.

3 | EC463 - B OS TON UNIVE R S ITY ELEC TR IC AL & COMPUTER ENGINE ER ING C AP S TONE S ENIOR DES IGN


Fig. 3. The mobile application that students can log into and monitor the temperature of their dormitories with. Users can also adjust the desired temperature range and notify their roommates of any changes.

4 COMPETING TECHNOLOGIES
Companies around the world have developed mechanisms to regulate heating systems for the purpose of reducing energy waste and providing a convenient method to alter the temperature of a room. The most significant products that provide such a service are the Bosch Smart Radiator, the Eve Thermo, and the Haverland Smartwave.
4.1 Bosch Smart Radiator
The UK company Bosch, developed a TRV (thermostatic radiator valve) that can be controlled through an internet connection. This TRV has the capability of being controlled with a voice assistant like Siri and can also be controlled by the smart home application that Bosch provides for their smart home products. This TRV also has buttons so that the temperature of the radiator can be controlled manually, and it carries a display that shows the temperature that the TRV is set to. There are also other features that are advertised such as a battery warning, a child safety lock, and a whisper mode. Bosch sells this device for approximately £55 [3]. This device is interoperable with other Bosch smart home devices such as their thermostats and door/window sensors. At that price point, Bosch not only provides a method to change the temperature from a web interface but an entire ecosystem. This ecosystem maintains the temperature automatically based on the information gathered by other Bosch smart home products and the user’s desired temperature.
4.2 Eve Thermo
The German company Eve has also developed a TRV that is capable of Internet of Things (IoT) functionality. Their product, marketed as “Eve Thermo,” is similar to the Bosch Smart Radiator. The Eve Thermo has a mobile application that is provided by Eve; however, it is only available on iOS. The TRV itself has an LED display that shows the set temperature, as well as tactile buttons that allow users to change the temperature manually, without the use of an internet connection. This device is being sold for £60 [4]. The Eve Thermo is compatible with other products sold by Eve, such as the Eve Door & Window, through the mobile application Eve provides. To achieve compatibility, all of Eve’s devices support Bluetooth and Thread for communication. For this compatibility to exist, the user must have an Apple TV (4th generation) or the HomePod mini, along with a mobile iOS device equipped with the Eve app. The mobile application provides a way of not only changing the temperature but also setting schedules so that a user can set different temperatures for different days in advance [5]. Thus, similarly to the Bosch Smart Radiator, Eve provides an ecosystem for their TRV, but that ecosystem is more limited due to the devices that can access the ecosystem. It provides a way for the user to plan out what they want for the temperature days in advance.
4.3 Haverland Smartwave
UK company Haverland have created an electric heater with similar “smart” capabilities to both the Eve Thermo and the Bosch Smart radiator. Their product named the “Haverland Smartwave” is a thin electric radiator (75 mm thick) that can be mounted on a wall. On the device, there are buttons (to change the temperature) and a LED display for the current temperature of the room. An important feature is that the Smartwave can detect sharp changes in temperature without the use of other devices, allowing it to change the heat output automatically. By default, the Smartwave does not have IoT capability and the user must purchase a “Smartbox” accessory separately to have IoT features [6]. However once the SmartBox accessory is installed, the Smartwave can be controlled on a mobile app (iOS and Android) and with Amazon Alexa. Currently, the Smartwave is being sold for £300 for the cheapest model, not including the SmartBox which will cost an additional £55 [7]. The mobile app for the optional SmartBox allows the user to schedule specific heating for different days, similar to the Eve Thermo. As an extension the app has a “learning” feature, where the app adjusts to a user's desired temperature based on previous usage [8]. The app also allows the user to view power consumption in correlation with the room temperature over a period of time (day, month and year). Our product will also record temperature data over a set time frame for a room although not on such a scale and detail as the Smartwave.
4.4 EcoSwitch
Our product is similar to our competitors in that we will allow the temperature of a room to be determined by user input on a web interface. There will also be data collection for the temperature of a room over a predetermined time period similar to the Smartwave and a low battery warning to alert the user like the Bosch Smart Radiator. While our competitor’s products require a specific heating system to be integrated into (e.g radiator heating), our product will be compatible with most heating systems that have a control unit. To achieve this, our product will be modular, with an attachment that will change depending on the design of the heating system’s control unit.

5 ENGINEERING REQUIREMENTS
This section breaks down the engineering requirements per associated subsystem.
5.1 Hardware
1. The device must be able to detect the room temperature and humidity levels with the DHT11 digital sensor whose range for relative humidity is 20-80%; for temperature is 0-50°C with ±2°C accuracy.[2]

4 | EC463 - B OS TON UNIVE R S ITY ELEC TR IC AL & COMPUTER ENGINE ER ING C AP S TONE S ENIOR DES IGN
2. The ESP32 microprocessor which can use the Arduino IDE
as the development environment must be able to read and
stream data to the clients. Also, the program is stored here
and it determines whether to turn on/off the actuator that connects to a programmable motor.
3. The swappable attachment should be in plastic and be able to cap the whole FCU dial nicely. Also, it should be attached with an actuator and allow a motor to give momentum to it. Moreover, this attachment must be easily removed and reattached to another FCU dial.
4. The device must support the removal of at least one sensor and its replacement with another sensor that uses the same communication protocol.
5. The actuator is the 28BYJ-48 Stepper Motor with ULN2003 driver which has 300 gf. cm pull in torque which is enough for turning the FCU dial back and forth.[9] The actuator must be installed inside the device and firmly attached to the attachment. Also, it is compatible with the ESP32 microprocessor. This motor set only costs $10, and easy installation makes the installation fee cheap.

5.2 Software
1. The device must be able to communicate with the user app via wifi connection or Bluetooth connection if wifi is disabled.
2. The cross-platform mobile app or full-stack web app must show the current room temperature and humidity. Also, it must allow the user to decide the temperature in a specific range.
3. An administrator website is needed to check the status of each device for maintenance purposes. Also, if the user changes the room temperature too many times in a short time, a warning message must be sent out to the user. If the user continues this kind of action, the administrator website must be able to overwrite the device and send out a report to the user.
4. The program designed in the microprocessor must be able to read the collected data and compare it with the database to set up a base value for maintaining the room temperature in a specific range.

5.3 Data Coll ection and Transmission
1. The digital sensor must send the room temperature and humidity data every five minutes. Also, it transfers the collected data to the microprocessor for comparison with the data in the database.
2. The input/request data of the app must be transferred through API via Node.js and React Native that acts as back end and front end servers respectively. The SQL database transfers data through servers to the app if that is a request or stored back to the database if there is an update.
3. The SQL database must be updated every day so that the the program can update its base value for maintaining room temperature.
4. The device must be able to transmit data wirelessly with a range of at least 1km and data rate of at least 250 kbps.

5.4 Power, cost and safety
1. The cost of this device should not exceed $100 because most of the compatible products are around that range. Also, its size should be similar to an FCU dial and light to prevent the dial from coming off.
2. The device should be powered by rechargeable batteries and the app should remind users of the battery level.
3. The device should be safe and stable (e.g., tamper-proof), and it should mount near the FCU.

6 APPENDIX A REFERENCES
[1] Zero waste plan. Zero Waste Plan | Sustainability. (n.d.).
Retrieved | October | 22, | 2021, | from
https://www.bu.edu/sustainability/projects/zerowaste-plan/.
[2] Industries, A. (n.d.). DHT11 basic temperature-humidity sensor + extras. adafruit industries blog RSS. Retrieved
October | 22, | 2021, | from
https://www.adafruit.com/product/386.
[3] Smart Radiator Thermostat. Bosch Smart Home. (n.d.). Retrieved October 22, 2021, from https://www.boschsmarthome.com/uk/en/products/devices/radiatorthermostat/.
[4] Eve Thermo. evehome.com. (n.d.). Retrieved October 22, 2021, from https://www.evehome.com/en/eve-thermo.
[5] Rowley, E. (2021, January 7). The best smart radiator valves 2021. Tech Advisor. Retrieved October 22, 2021, from https://www.techadvisor.com/test-centre/digitalhome/best-smart-radiator-valves-3693855/.
[6] Haverland SmartWave self-programming electric radiators. Haverland SmartWave Self-Programming Electric Radiator. (n.d.). Retrieved October 22, 2021, from https://www.electricradiatorsdirect.co.uk/haverlandsmart-wave-electric-radiators-white/.
[7] Haverland SmartWave Electric Radiators - SmartBox WIFI Hub. Haverland SmartWave Electric Radiator SmartBox Controller. (n.d.). Retrieved October 22, 2021, from https://www.electricradiatorsdirect.co.uk/haverlandsmart-box-wifi-controller/.
[8] Haverland app - step by step - electricradiatorsdirect.co.uk.
(n.d.). | Retrieved | October | 22, | 2021, | from
https://www.electricradiatorsdirect.co.uk/media/pdf/Smartbox_Haverland_App.pdf?_t=1536576385.
[9] Components101 - 28BYJ-48 - 5V Stepper Motor.Retrieved
October | 22, | 2021, | from
https://components101.com/motors/28byj-48-steppermotor

5 | EC463 - B OS TON UNIVE R S ITY ELEC TR IC AL & COMPUTER ENGINE ER ING C AP S TONE S ENIOR DES IGN

Client Signature:

____________ | ________________

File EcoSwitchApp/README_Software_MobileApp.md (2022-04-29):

# <div id="top">EcoSwitch Mobile Application</div>

## Table of Contents
  <ol>
    <li>
      <a href="#about-the-project">About The Project</a>
    </li>
    <li>
      <a href="#software-module-overview">Software Module Overview</a>
      <ul>
        <li><a href="#appjs">App.js</a></li>
        <li><a href="#stylesjs">styles.js</a></li>
      </ul>
    </li>
    <li>
      <a href="#dependencies-between-modules">Dependencies Between Modules</a>
    </li>
    <li>
      <a href="#development-and-build-information">Development and Build Information</a>
    </li>
    <li>
      <a href="#getting-started">Getting Started</a>
      <ul>
        <li><a href="#prerequisites-installation">Prerequisites Installation</a></li>
        <li><a href="#usage">Usage</a></li>
      </ul>
    </li>
  <li>
      <a href="#contact">Contact</a>
    </li>
  </ol>

## About The Project
<p align="justify">
  One of the original desired deliverables given by the client is a cross-platform mobile application that students can use to monitor and manage the   temperature in their rooms. Students can log in using their given BU email and view their associated information.
</p>

<p align="right">(<a href="#top">back to top</a>)</p>

## Software Module Overview

<p align="justify"> Currently, the application has one main module that contains all functionality. While this is bad practice, it was Keven's first time using React Native for a large scale project and due to time constraints he could not reorganize the code. </p>

### App.js
The driving module for the mobile application. Developed using the React Native Framework and Javascript. This module includes three screens for the user to navigate through, each detailed below.

#### Login Screen
<p align="justify"> This is where users will sign in with their given BU email account, using Google Authentication to secure the interaction. The app prevents any emails outside of the proper domain (@bu.edu) from signing into the application. This feature was implemented as an extra authentication step since only BU students should be using the application. </p>

<div align="center">

</div>

#### Main Screen
<p align="justify"> This screen displays the current temperature and humidity reported by the user's assigned device. The information is fetched from our backend database based off of the user login. The values presented to the user refreshes every 10 seconds in the development build, but will be changed to every 5 minutes for production. Users can also set a desired temperature for their room, which the device will adapt to accordingly. </p>

<div align="center">

</div>

#### Credits Screen
<p align="justify"> A simple screen displaying the names of the project contributors. Accessed through tapping the logo in the upper-right corner. </p>

<div align="center">

</div>

### styles.js
<p align="justify"> A separate JavaScript file that contains all the formatting for different elements in each screen render. </p>

<p align="right">(<a href="#top">back to top</a>)</p>

## Dependencies Between Modules

Below is a simple flow diagram of the different pages used in App.js, how they interact with one another, and some functions of each where applicable.

<div align="center">

</div>

## Development and Build Information
All installed dependencies for the project can be found within the [package.json](https://github.com/mharkess/EcoSwitch/blob/main/EcoSwitchApp/package.json) and [package-lock.json](https://github.com/mharkess/EcoSwitch/blob/main/EcoSwitchApp/package-lock.json) files found within this directory.

Developed and built using the following programs and versions:

- [NodeJS v14.17.6](https://nodejs.org/en/download/)
- NPM v6.14.15
- [Expo v4.12.11](https://docs.expo.dev/get-started/installation/)

<p align="right">(<a href="#top">back to top</a>)</p>

## Getting Started

### Prerequisites Installation

Install the software mentioned above in the [Development and Build Information](#development-and-build-information) section. This varies per system and operating system. Please refer to the respective websites for further installation information.

Once repository is cloned, navigate to this directory (.../EcoSwitch/EcoSwitchApp) and run the following code to automatically install dependencies from package.json:

```sh
npm install
```

Alternatively, the following also works:

```sh
expo install
```

### Usage

For development mode, use Expo and ExpoGo.
1. In the project directory, start the session with the following command:

```sh
expo start
```

2. With mobile device with ExpoGo installed, scan the provided QR code and open the application.

**OR**

1. Access the project pre-production build, hosted using Amplify. 
    - [LINK](https://main.d2yjkgcqrgxtij.amplifyapp.com/)
    - Please note that this build does not work properly at this time.

<p align="right">(<a href="#top">back to top</a>)</p>

## Contact

If there are any further questions about the application project, please contact the lead developer via email.
- kevend@bu.edu
- kedeoliveira7@gmail.com

<p align="right">(<a href="#top">back to top</a>)</p>

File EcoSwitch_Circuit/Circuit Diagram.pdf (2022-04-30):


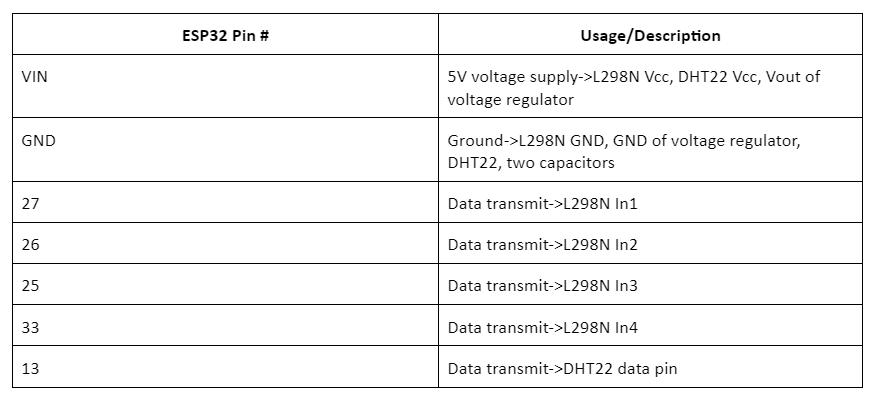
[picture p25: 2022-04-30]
EcoSwitch_Circuit/Hardware Pinout.png

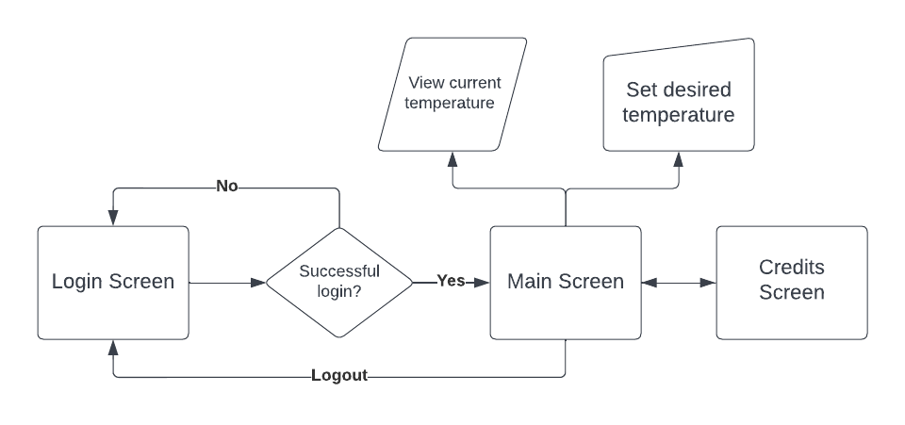
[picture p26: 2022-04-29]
EcoSwitchApp/images/flowchart.png

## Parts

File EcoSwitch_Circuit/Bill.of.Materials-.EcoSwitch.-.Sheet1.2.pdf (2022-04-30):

Bill of Materials

General Type | Part Name | Quantity Function | Finish | Manufacturing Process Relevant Dimensions
Attachment | Attachment | 1 turn the physical switch | high temp plastic | 3d printed | 35 x 35 x 35 mm
| motor holder | 1 Protect the actuator | high temp plastic | 3d printed | 50 x 50 x 41 mm
Controls | ESP32 | 1 microcontroller to control switch functions
https://www.amazon.com/Aideepen-Digital-Temperature-Humidity-Monitor/dp/B07XBRMN4P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 DHT22 | 2 temperature and humidity sensor *updated for quality | soldering
https://www.amazon.com/CO-RODE-Battery-Holder-Wired-Switch/dp/B00VE7HBMS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 12V battery pack | 1 holds the batteries
https://www.amazon.com/STEPPERONLINE-Stepper-63-74oz-Connector-Extruder/dp/B07LF898KN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 stepper motor | 1 motor to rotate switch
https://www.amazon.com/Controller-H-Bridge-Stepper-Control-Mega2560/dp/B07WS89781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 L298N motor drive controller | 1 motor driver board
https://www.amazon.com/Duracell-CopperTop-Alkaline-Batteries-Count/dp/B002UXRXEG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 AA batteries | 8 power the circuit
Rubber strip | 1 hold the attachment tightly on the switch | rubber
10K ohm resistor | 1
voltage regulator 5v | 1
100nF ceramic capacitor | 1
1uF Electrolytic capacior | 1
https://www.amazon.com/GeeekPi-Character-Backlight-Raspberry-Electrical/dp/B07S7PJYM6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 LCD Display | 1 Display temperatures
Heat sink | 1 absorb heat created from voltage regulator

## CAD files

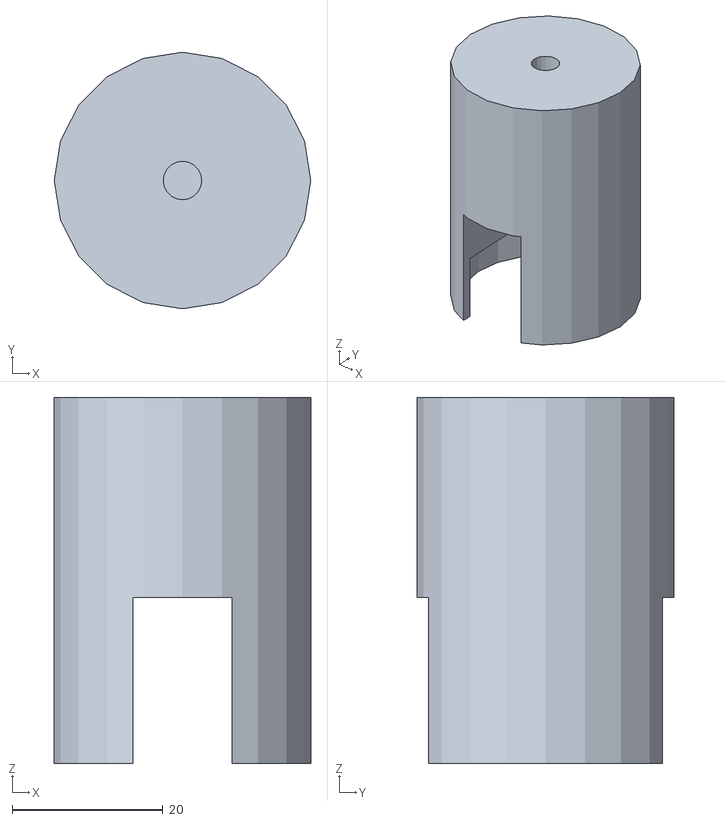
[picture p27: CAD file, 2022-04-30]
EcoSwitch_attachmen/Ecoswitch_attachment.stl
34.0 x 34.0 x 48.5

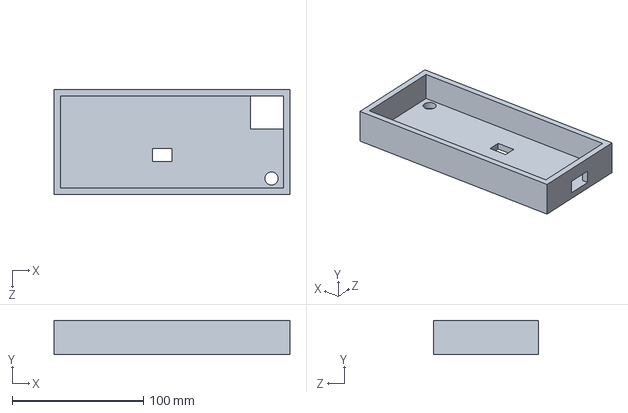
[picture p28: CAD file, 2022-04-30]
EcoSwitch_Casing_and_install/toppart.SLDPRT
180.0 x 26.0 x 80.0 mm

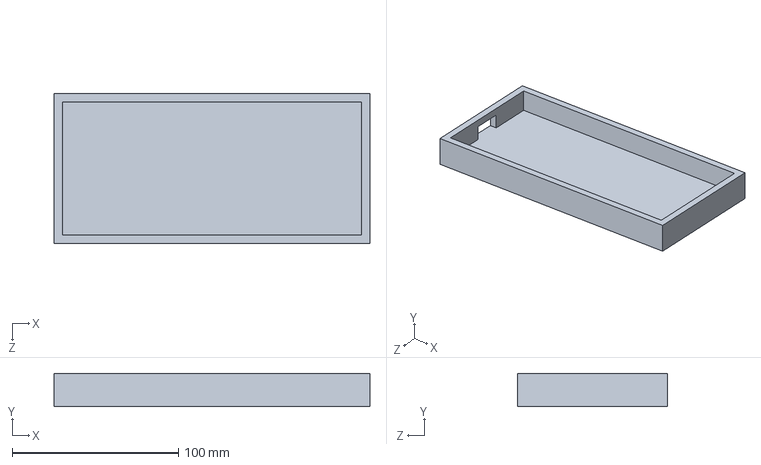
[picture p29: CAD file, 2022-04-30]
EcoSwitch_Casing_and_install/boxbase.SLDPRT
190.0 x 20.0 x 90.0 mm

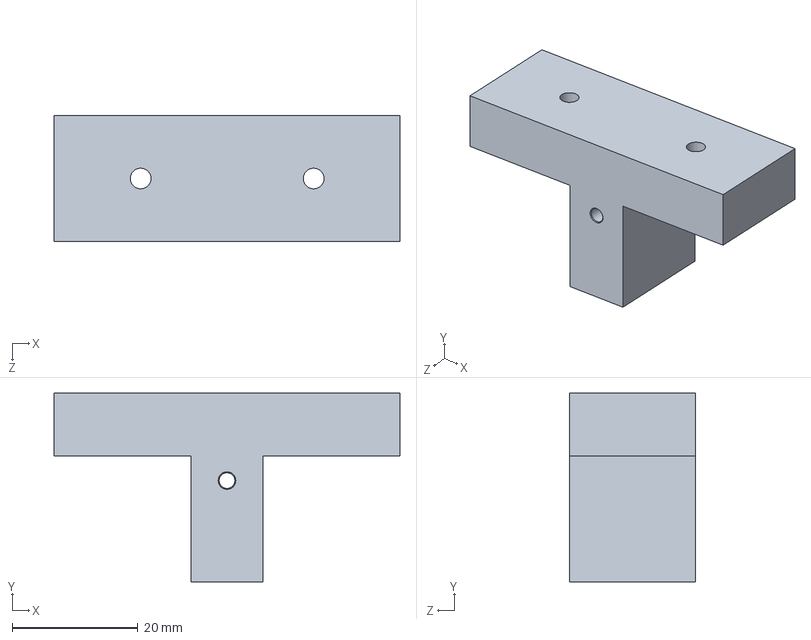
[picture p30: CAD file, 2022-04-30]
EcoSwitch_Casing_and_install/Part2.SLDPRT
55.0 x 30.0 x 20.0 mm

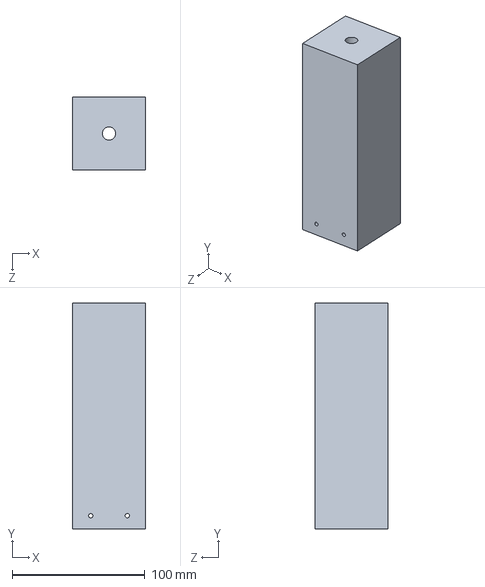
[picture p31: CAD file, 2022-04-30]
EcoSwitch_Casing_and_install/Part1.SLDPRT
55.0 x 170.0 x 55.0 mm

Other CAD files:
EcoSwitch_Casing_and_install/Part1_draw.SLDDRW
EcoSwitch_Casing_and_install/Part2_draw.SLDDRW

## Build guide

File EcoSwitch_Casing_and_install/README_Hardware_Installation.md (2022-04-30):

# EcoSwitch Installation and Casing
## Table of Contents
  <ol>
    <li>
      <a href="#about-the-project">About The Project</a>
    </li>
    <li>
      <a href="#hardware-module-overview">Hardware Module Overview</a>
    </li>
    <li>
      <a href="#designing-the-casing-for-the-device">Designing the Casing for the Device</a></li>
    </li>
    <li>
      <a href="#ecoSwitch-device-installation-steps">EcoSwitch Device Installation Steps</a>
    </li>
  <li>
      <a href="#contact">Contact</a>
    </li>
  </ol>

## About the Project
<p align="justify">The EcoSwitch device's installation involves assembling and mounting it on the Fan Control Unit (FCU). The original problem statement required the EcoSwitch device to be safely mounted on the FCU dial and tamperproof.</p>

Device Concept:

device concept<p align="justify">

<p align="right">(<a href="#top">back to top</a>)</p>

## Hardware Module Overview
<p align="justify">The device comes with a battery pack connected to a rectangular box which is the circuit and driver for the device. Also, there should be another longer rectangular box with four M4 screws and two M3 screws. The installation steps below show how to assemble the whole device and mount it on the top of the FCU dial. Also, instructions for designing these boxes are listed below.</p>

<p align="right">(<a href="#top">back to top</a>)</p>

### Designing the Casing for the Device
<p align="justify">All the designs are done using 3D modeling in Solidworks. The first part is the case for the stepper motor. The purpose of this case is to stabilize the stepper motor when it turns. Therefore, the inner square dimension for the case should be close to the overall dimension of the stepper motor with around 10% tolerance for the error in 3D printing. Also, there should be holes besides for screws to stabilize it and spaces for the wire to come out of the case. The 3D model for this case is here: <a href="https://github.com/mharkess/EcoSwitch/blob/main/EcoSwitch_Casing_and_install/Part1.SLDPRT">casing_for_motor</a>. The drawing of this 3D model is here: <a href="https://github.com/mharkess/EcoSwitch/blob/main/EcoSwitch_Casing_and_install/Part1_draw.SLDDRW">drawing_case_for_motor</a>.</p>

<p align="justify">The following diagram is a perpective view for this case:</p>

<div align="center">

</div>

<p align="justify">The motor case is connected with two T-bars beside for stabling the whole device in the two pivots point near the FCU device. The actual FCU device looks like the following diagram with a red circle as the pivot point:</p>

<div align="center">

</div>

<p align="justify">The T-bar has a hole on the top which should be the same size as the pivot holes. Also, two holes beside should have the same dimensions as the side holes in the motor case. The 3D model for the T-bar is here:<a href="https://github.com/mharkess/EcoSwitch/blob/main/EcoSwitch_Casing_and_install/Part2.SLDPRT"> 3Dmodel_for_T_bar</a>. The drawing of the T-bar is here: <a href="https://github.com/mharkess/EcoSwitch/blob/main/EcoSwitch_Casing_and_install/Part2_draw.SLDDRW">Drawing_for_T_bar</a>. The following diagram is a perspective view for this T-bar:</p>

<div align="center">

</div>

<p align="justify">The second case is used to cover the whole circuit and driver. It connects with battery outside and motor in the motor case. The 3D model for the base part of circuit case is here:<a href="https://github.com/mharkess/EcoSwitch/blob/main/EcoSwitch_Casing_and_install/Part2.SLDPRT"> 3Dmodel_for_circuit_case_base</a> and the top part is here:<a href="https://github.com/mharkess/EcoSwitch/blob/main/EcoSwitch_Casing_and_install/toppart.SLDPRT"> 3Dmodel_for_circuit_case_top</a>. The isometric view of the case is as follow: </p>
  
  

<p align="right">(<a href="#top">back to top</a>)</p>

## EcoSwitch Device Installation Steps
<p align="justify">Each EcoSwitch device will come prebuilt with a motor, an attachment, a circuit board within the rectangular outer shell, and a battery pack. The device will be mounted on the FCU dial and securely attached to the knob. Then, batteries are needed in the battery pack to power the device and assemble it as follow:</p>

1. Put two T-shape bars beside the rectangle box. 
2. Use four M4x20 mm screws and drill them inside the two holes of the T-shape bars. Also, fix the M4 screw locks at the end to stabilize the screws.
3. Use two M3x20 mm screws to drill on the top hole of the two T-shape bars.
4. Fix the M3 screw locks at the end to stabilize the screws.

<p align="right">(<a href="#top">back to top</a>)</p>

## Contact
If there are any further questions about the application project, please contact the lead developer via email.
- liaophie@bu.edu

<p align="right">(<a href="#top">back to top</a>)</p>

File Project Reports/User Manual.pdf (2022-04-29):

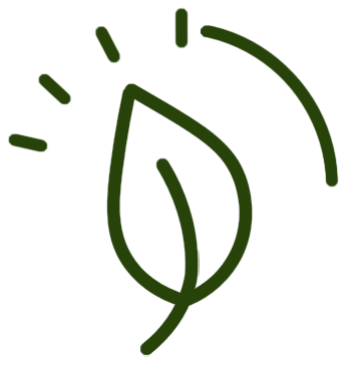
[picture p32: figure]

Team 31 (Team EcoSwitch) | March 25, 2022

Boston University
Electrical & Computer Engineering EC464 Capstone Senior Design Project User's Manual
EcoSwitch

Submitted to

Harshavardhan Ogoti
State Street Global Advisors 1 Iron St, Boston MA 02210 hogoti@bu.edu

by
Team 31
Team EcoSwitch

Team Members
Keven DeOliveira kevend@bu.edu Samarah Uriarte samcu@bu.edu Michael Harkess mharkess@bu.edu Michelle Thevenin thevenin@bu.edu Jiawei Liao liaophie@bu.edu

Submitted: 4/18/2022

User's Manual | 2

### 1. EcoSwitch

### 2. Table of Contents

Executive Summary | 2
1 | Introduction | 3
2 | System Overview and Installation | 4
2.1 | Overview block diagram | 4
2.2 | User interface | 6
2.3 | Physical description | 7
2.4 | Installation, setup, and support | 8
3 | Operation of the Project | 11
3.1 | Operating Mode 1: Normal Operation | 11
3.2 | Operating Mode 2: Abnormal Operations | 13
3.3 | Safety Issues | 14
4 | Technical Background | 15
5 | Relevant Engineering Standards | 17
6 | Cost Breakdown | 18
7 | Appendices | 19
7.1 | Appendix A - Specifications | 19
7.2 | Appendix B – Team Information | 20

2.

### 3. Executive Summary

Manually controlled FCUs (fan coil units) in BU brownstone dorms lead to rooms becoming uncomfortably warm due to its inefficiency. As a result, students either turn off their heating unit or open a window in order to regulate their dormitory conditions. These methods are either inconvenient to the student or waste energy. As a solution, we propose EcoSwitch, a system consisting of a smart device networked with online portals to allow students and administrators to monitor and adjust the temperatures of these rooms. EcoSwitch will establish applications that can help Boston University achieve its Zero Waste goals while increasing the students’ quality of life.

### 1 Introduction

Many of the brownstones on the Boston University campus have a heating system that is a manually controlled fan coil unit, also known as an FCU. The FCU works by heating up air with a coil and circulating that air in the room with a fan. It is controlled through a dial on the FCU unit with simple settings such as low, medium, high, and off. These preset settings cause students to switch their units on and off or open a window to release some of the overgenerated heat. The constant switching becomes an inconvenience to students and a waste of energy for the university.
The device’s hardware requirements include safe mounting on the FCU, a swappable attachment that connects to the dial, and tamper-proof features so that it remains in the dorm. On the software side, students should be able to monitor and change their dorm room temperatures on a cross platform mobile app, and building maintenance should have access to an administrator website that they can use to monitor all dorms through the EcoSwitch devices.
As a solution to these issues, we proposed EcoSwitch. EcoSwitch is a smart device that allows for user interaction through a mobile app and website, features that are typical to smart home systems. The device controls room temperatures based on user specifications submitted through the app for desired temperatures. The mobile application displays the temperature of the dorms to both students and housing administrators. The website, which is for the latter, allows them to monitor all units. These features will allow our system to create the most comfortable temperatures for students through a convenient and efficient process which will ultimately reduce energy waste. EcoSwitch will help BU reach their mission to achieve zero waste by 2030. Our solution is cost-effective and compatible with the existing heating infrastructure in the brownstones.
EcoSwitch resolves the aforementioned problems by automating the process of changing dorm temperatures. By doing so, EcoSwitch can keep the temperature of a room consistent. When a user inputs a temperature, EcoSwitch will turn the switch of the FCU to keep the temperature as close to that value as possible. If the student is comfortable, there will no longer be a need to open a window or change the temperature as dorm conditions inevitably drift away from that preferred temperature. EcoSwitch also takes humidity and local weather conditions into account to ensure that the room is within an acceptable range of the user's chosen temperature.
EcoSwitch will also determine if an FCU is failing in a particular dormitory. Administrators will be able to observe this from the temperature and humidity trends shown in the graph within the website. It can therefore inform facility workers of the issue immediately.
Administrators will be able to add students to the appropriate EcoSwitch devices based on the students’ housing assignments, as well as remove them from those residences once the students have moved out. New residents will have to simply sign up on the app and immediately be able to connect to their devices upon move in.
The remainder of this document includes information on the system, installation, operation, and safety of the EcoSwitch device. It is worth noting that there were technical issues with the device’s ability to rotate the FCU dial due to the high torque that the dial requires to be turned. The motor we currently have integrated into the circuit cannot overcome this torque, but the rest of the system and the logic behind the device’s operation works as intended.

### 2 System Overview and Installation

This section will cover the overall structure of the EcoSwitch system as well as how to set up each of its main components.

### 2.1 Overview Block Diagram

The EcoSwitch system can be generalized into three main components: the EcoSwitch device, the administrator website, and the student mobile app. Figure 2.1.1 contains the block diagram for the overall system, demonstrating how the aforementioned components communicate and interact with each other. While sensor data is being fed to both the administrator website and the student mobile app, it is worth noting that the latter will only have access to the data that is being retrieved from their residence's corresponding device.

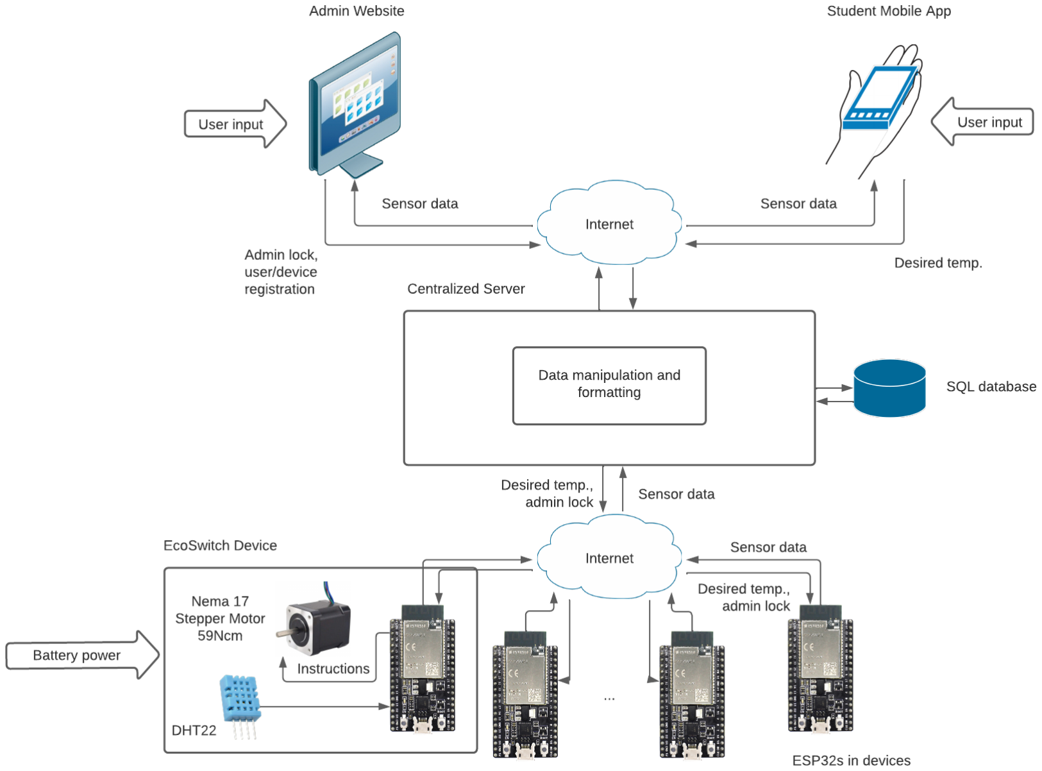
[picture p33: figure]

Figure 2.1.1 High-level block diagram of the entire EcoSwitch system, including the device, mobile application, and website. Some electrical components are left out for simplicity.
The EcoSwitch device’s logic is available in greater detail in Figure 2.1.2. We have not included the conversion to actuator instructions in this block diagram because it takes place in the ESP32 script rather than in the server.

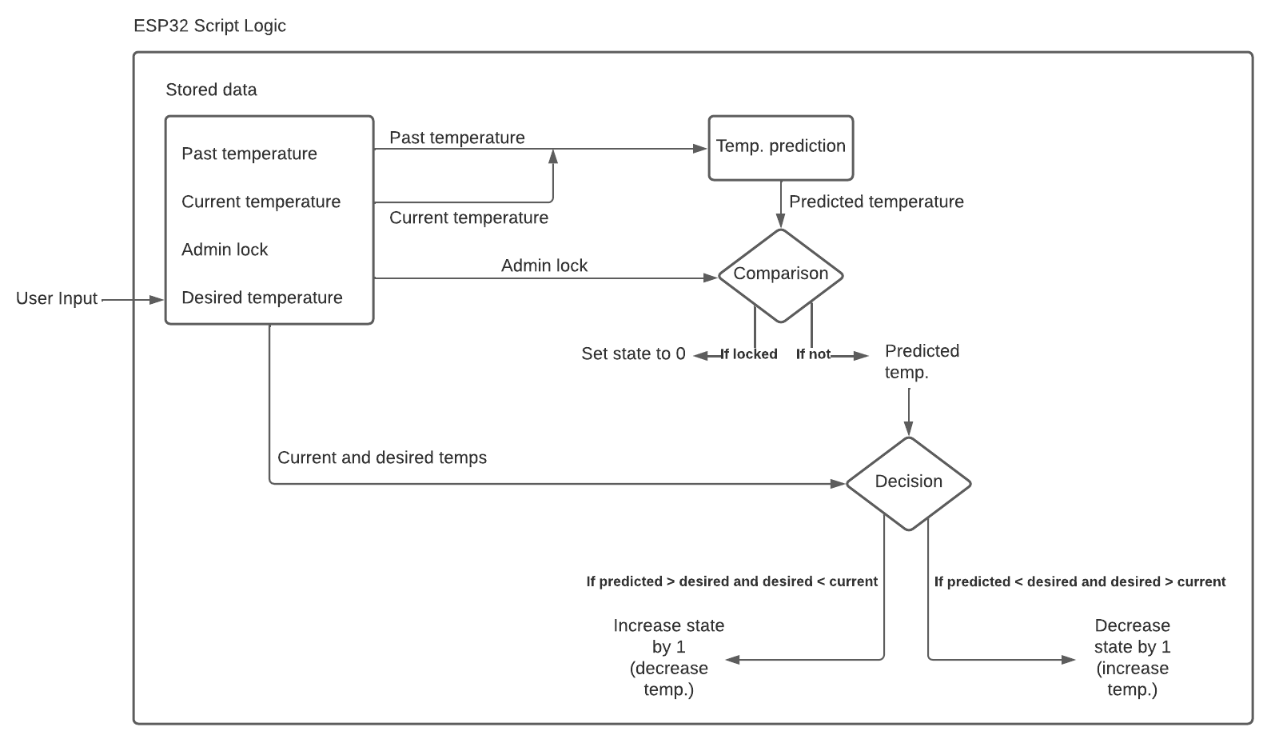
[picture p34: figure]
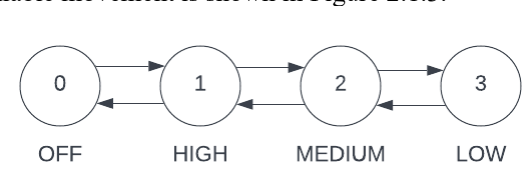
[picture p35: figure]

Team 31 (Team EcoSwitch) | March 21, 2022

Figure 2.1.2 The EcoSwitch device’s block diagram, illustrating the logic that will be operating on all devices and connecting them to their users’ input. The admin lock input is set by the housing administrator through the “Device Adjustment” page on the website. If an administrator indicates all the FCUs in a building should be turned off by submitting the appropriate form, students cannot overwrite that decision by setting the desired temperature through the app. Furthermore, temperature predictions are calculated in this script with equation 2.1.1, where the change in temperature is evaluated by subtracting a previous temperature from the current one.
(2.1.1)
The device’s logic is based on an emulation of the settings on the FCU dial, which are enumerated by states 0 through 3. State 0 is off, 1 is high, 2 is medium, and 3 is low. Additionally, the dial has restricted movement, as it cannot turn completely around and must instead move through the existing states to reach another one. We have taken this into account in our design, and the simplified state machine for this available movement is shown in Figure 2.1.3.

Figure 2.1.3 This is the only way the EcoSwitch device can move between states.

### 2.2 User Interface

The UI includes the administrator website as well as the mobile application to be used by students. Figure 2.2.1 shows the three pages of the mobile app: the login page, the main page, and the credits

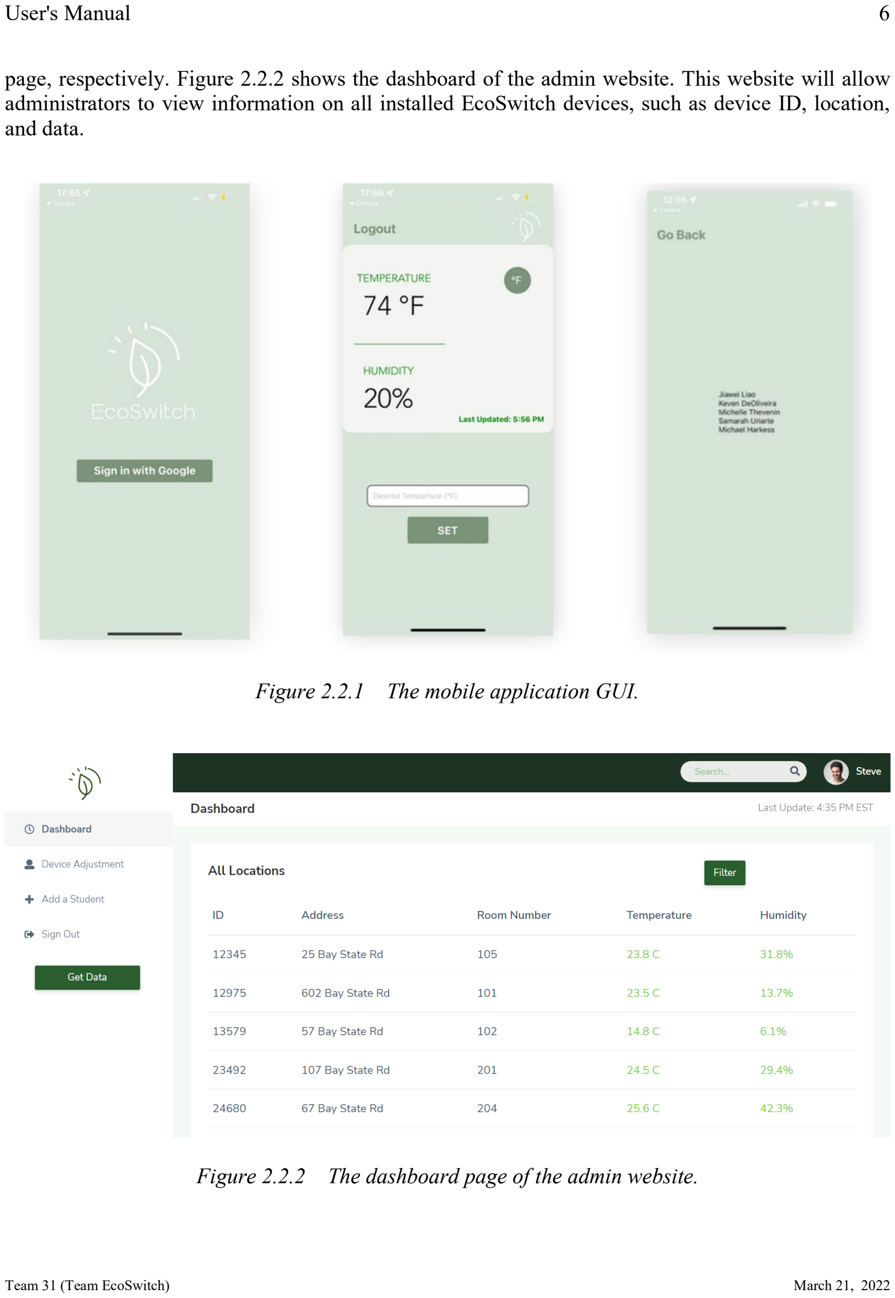
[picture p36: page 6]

page, respectively. Figure 2.2.2 shows the dashboard of the admin website. This website will allow administrators to view information on all installed EcoSwitch devices, such as device ID, location, and data.

Figure 2.2.1 The mobile application GUI.

Figure 2.2.2 The dashboard page of the admin website.

### 2.3 Physical Description

The physical EcoSwitch device consists of a circuit connected to the motor, an attachment, and an outer shell. The motor directly connects to the attachment to turn the dial switch while the other components of the circuit rest inside the outer shell. The outer shell is connected to the FCU surface without making contact with the dial. This design allows the motor and connected attachment to turn freely while providing stability to the overall device.

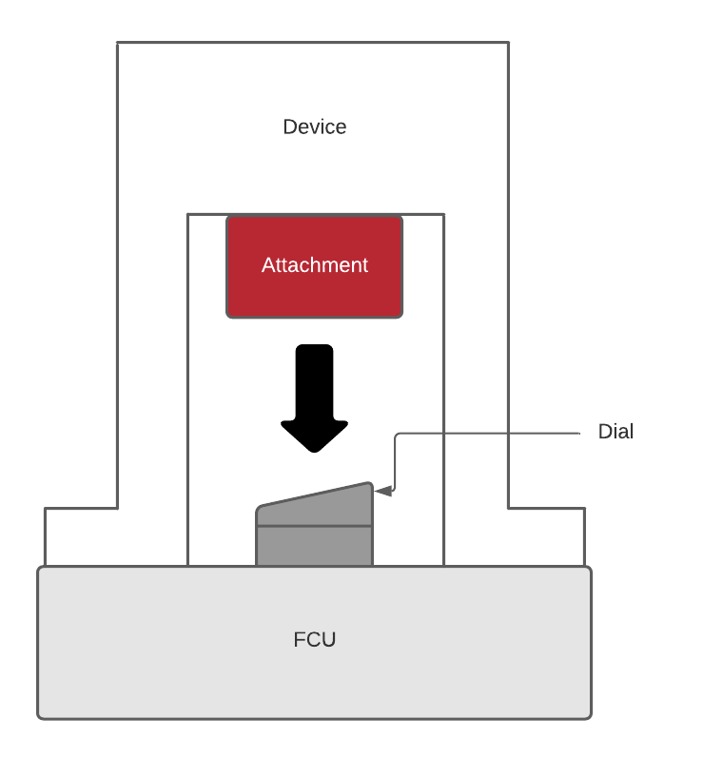
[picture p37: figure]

Figure 2.3.1 The EcoSwitch concept that illustrates how the device attaches to the FCU dial switch.
The EcoSwitch circuit consists of an ESP32 microcontroller, a DTH22 temperature and humidity sensor, a L298N motor driver, a Nema 17 stepper motor, an LCD screen, and a 12V battery pack with 8 AA alkaline batteries. It also includes a 5V regulator, a 10 kΩ resistor, an 100 nF ceramic capacitor, and a 1uF electrolytic capacitor. Figure 2.3.2 demonstrates how the circuit is put together.

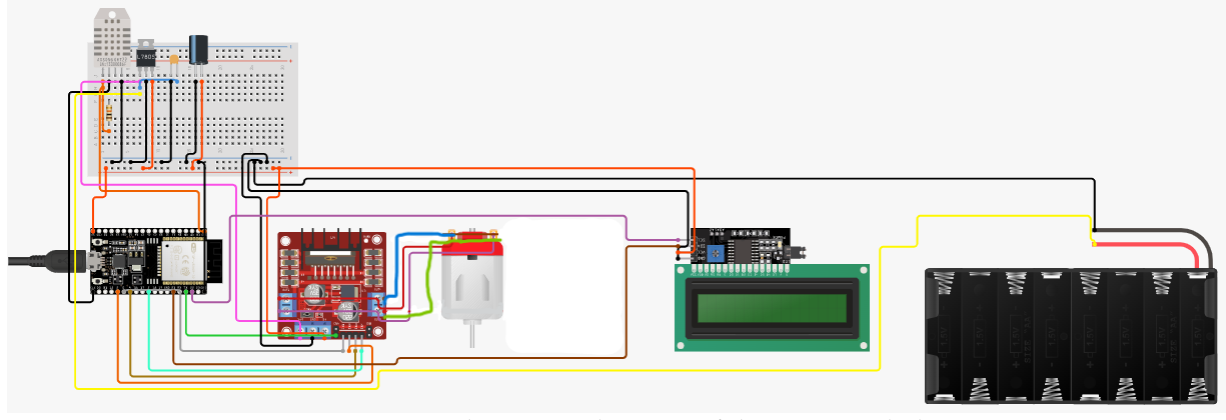
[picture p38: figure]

Figure 2.3.2 The circuit diagram of the EcoSwitch device. The bottom of the attachment is specifically designed to fit on top of the FCU switch in order to turn the dial with the motor. The hole at the top of the attachment is fit to the diameter of the motor shaft.

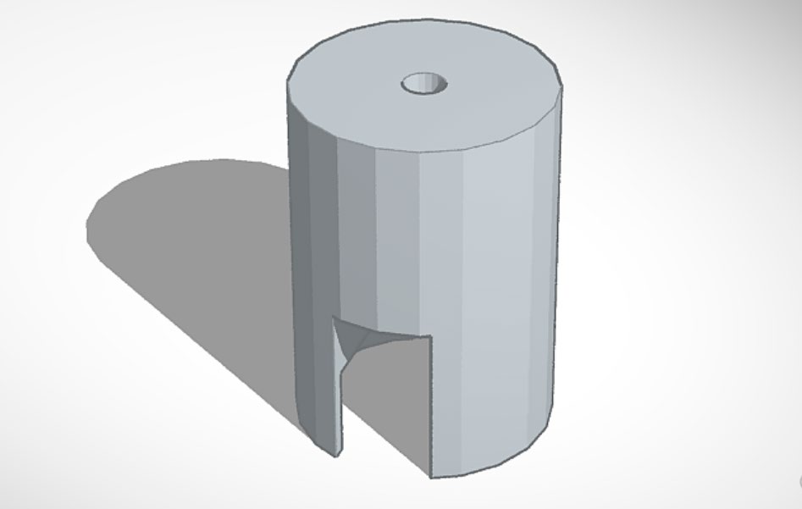
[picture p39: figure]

Figure 2.3.3 The FCU switch attachment. The outer shell of the device is used to apply a downward force on the motor so that it stands still enough to apply the full torque onto the switch.

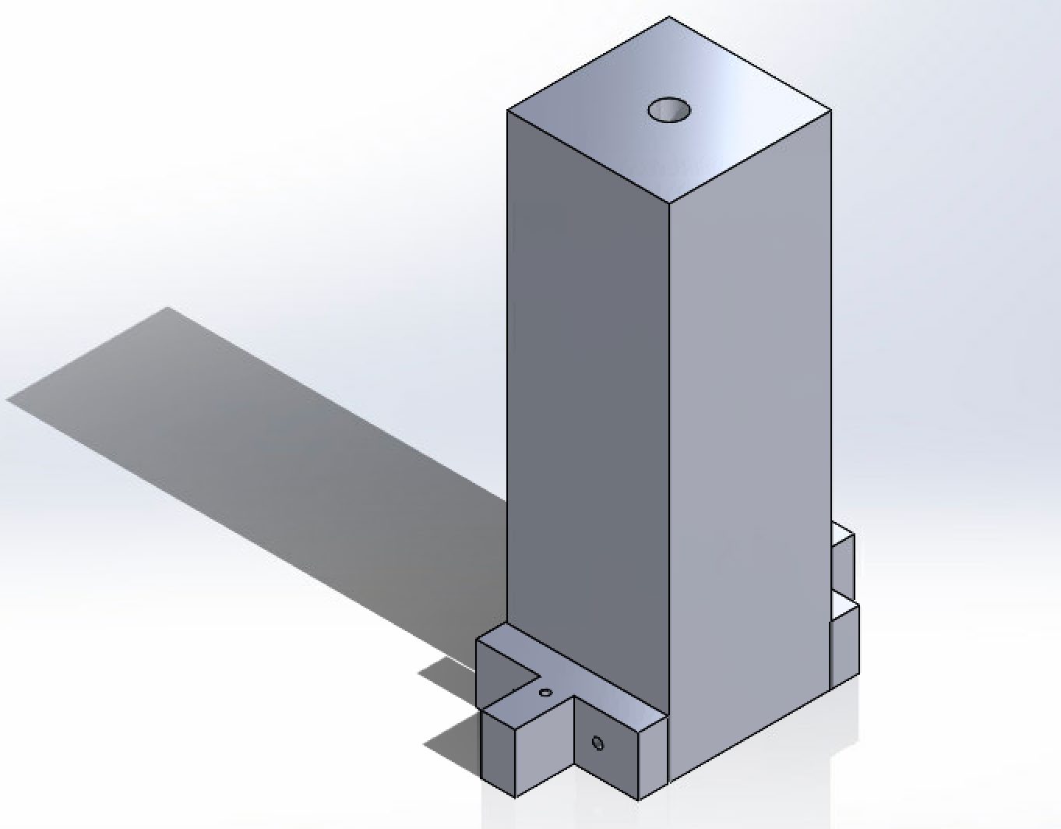
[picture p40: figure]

Figure 2.3.4 The EcoSwitch device’s outer shell.

### 2.4 Installation, Setup, and Support

Each EcoSwitch device will come prebuilt with a motor, an attachment, a circuit board within the rectangular outer shell, and a battery pack. The user needs to mount the device on the FCU dial, making sure that the attachment is securely attached to the knob. Then, the user needs to put batteries in the battery pack to power the device and assemble it as follows:
1. Put two T-shape bars beside the rectangle box.
2. Use four M4x20 mm screws and drill them inside the two holes of the T-shape bars. Also, fix the M4 screw locks at the end to stabilize the screws.
3. Use two M3x20 mm screws to drill on the top hole of the two T-shape bars.
4. Fix the M3 screw locks at the end to stabilize the screws.

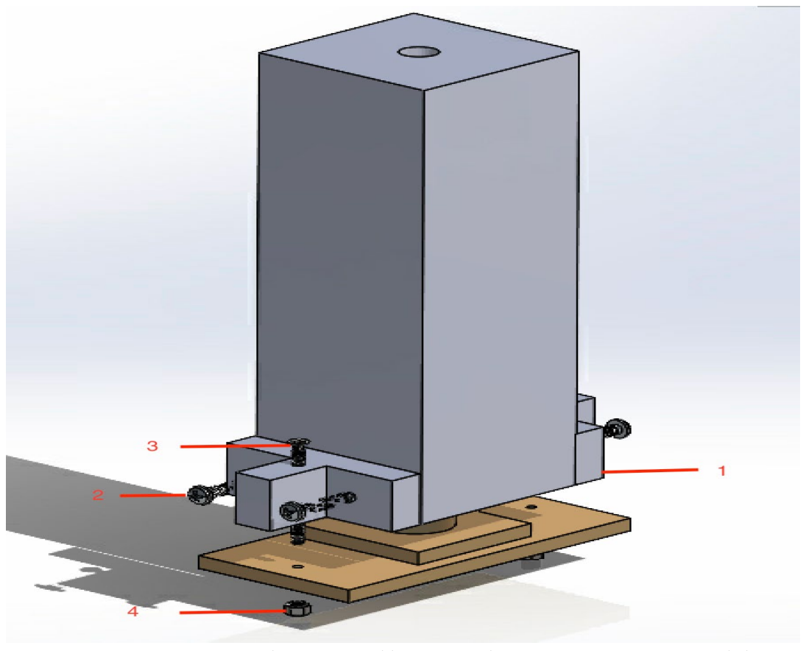
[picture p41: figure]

Figure 2.4.1 The installation diagram in assembly. To maximize the functionality of the EcoSwitch system, the user should consider several factors. The EcoSwitch device is an IoT device that requires internet connectivity. Therefore, it would be ideal to have it positioned at a location with a stable WiFi connection. Also, the EcoSwitch device contains a temperature and humidity sensor inside the insulator, as well as other electrical components. Consequently, the users should not bring any external heat or water source near the device. For example, if the user wants the EcoSwitch device in the kitchen, it should not be right next to the sink in case of a leakage or other emergencies that may cause the device to malfunction.
Setup:
1. For facility workers: register the device through the website by scanning the barcode contained in the packaging and entering the requested information. We are unable to implement this portion of the setup process because it requires a larger scale of production; however, it is included to provide a better understanding of the overall product. Then, assemble and install the EcoSwitch device onto the FCU dial and surface.
2. For students: download the EcoSwitch mobile application from the appropriate app store and sign up using a Google account.
3. For administrators: navigate to the website and sign up using a Google account or an email and password.
Support:
The user might find EcoSwitch intimidating due to the sensors and motors inside the device. Therefore, we provide an interactive mobile application and website. The mobile application allows the user to see the current room temperature and humidity levels and the battery level. The website also offers this functionality, except it includes this data for all EcoSwitch devices, rather than just one.

### 3 Operation of the Project

This section includes details on the operation of the EcoSwitch system under two modes: normal and abnormal. In addition, safety issues that may occur during either of these aforementioned operations will be discussed.

### 3.1 Operating Mode 1: Normal Operation

A detailed description of the system’s operating mode, as well as its consequences and results, is provided below.
a. | 3.1.1 | Operating Mode in Detail
We will not be implementing the components that are required to complete this procedure. This is due to our limited number of existing EcoSwitch devices. However, we have developed the process that facility workers will be able to follow to set up the EcoSwitch device and provided it in detail below:
1. Connect the device to BU WiFi by using a smartphone with Bluetooth capabilities. To do this, the user must allow the EcoSwitch device to pair with the smartphone after Bluetooth is turned on. Then, the user can simply follow the directions that are shown on the smartphone screen.
2. Register the device by using their smartphone to scan the barcode that will be available in the device’s packaging.
3. Enter the location the device will be stationed at in the form that the barcode connects the user to.
4. Ensure there is no error in the verification process that attempts to check that the EcoSwitch device does not already exist in the database and that the residency is valid (ensuring it contains an FCU to control).
Otherwise, students may view the device’s battery monitor or numerical display to access information about the device’s battery levels or their dormitory’s temperature levels, respectively.
Student users can access the mobile application functionalities, mentioned in 3.1.3 with the following steps:
1. Sign in using any Google email account through Google Authentication.
2. Gain access to their assigned device’s data reading via the main menu.
3. Adjust the temperature scale.
4. Set a desired temperature range for the room.
The user can access the website functionalities, as mentioned in section 3.1.3, with the following steps:
1. Enter the URL for the website; this will bring users to the home page.
2. Navigate to the “Administrator Portal” login page.
3. Log in using their Gmail account or the email and password they have used to sign up.
4. View the dashboard and scroll down to see the graphs that show trends in data.
5. Navigate to the sidebar and click the functionality of interest.
6. For the “Device Adjustment” page, in order to turn off all the FCUs in one location, enter the address of the building and click the button below to make the request. This will lock that residence and prevent students from being able to control any devices in it. To unlock the location, navigate to the appropriate tab and enter the address of the building they wish to unlock. Then, click the button below to make the request.

7. For the “Add a Student” page, enter the student’s BU email address, residence, and room number, and then click the button below to make the request. To remove a student, repeat these steps but on the appropriate tab.
8. Click the profile icon in the upper right corner of the page to access profile information.
9. Once finished, the user can click “Sign Out.”
b. | 3.1.2 | User Interface
The user interface will vary depending on the role of the user: students will have access to the mobile application, and administrators, including facility workers, will have access to the website as well as the device setup interface. The former two UI options are pictured above in the User Interface (2.2) section of this manual.
The device setup interface is still a work in progress. Currently the setup process allows admins to set up a WiFi connection to the device, or factory reset the device.
c. | 3.1.3 | Normal Consequences of User Actions
For student users, the mobile application will allow the following:
1. Secure login using a valid Google account.
2. Viewing recently observed (within the past 5 minutes) temperature and humidity data.
3. The ability to set a desired temperature/temperature range.
For housing administrators, the website will allow the following:
1. Secure login using a valid Google account or an email and password.
2. View device information such as ID, location, data for every installed EcoSwitch device.
3. Turn off all the FCUs in a specified location, effectively locking it so students cannot control the EcoSwitch devices it contains.
4. Manually assign and remove students to and from devices.
5. Register and verify new devices.
a. Note: This feature cannot be implemented until more Ecoswitch devices are created. The concept, however, describes our solution to guarantee an easy setup process.
Also for administrators, including facility workers, the device configuration interface will allow the following:
1. Set up WiFi connection for a device.
2. Factory reset the device.
3. Wirelessly complete setup for a device.
d. | 3.1.4 | Potential Abnormal Results
Due to the unstable nature of BU WiFi, the EcoSwitch device may randomly go offline. In this situation, the device will attempt to reconnect to BU WiFi until it successfully does so or until it is turned off. This process may interfere with the device’s ability to send the data it has most recently recorded to the server, resulting in the temperature and humidity database containing outdated values. Additionally, the device cannot be controlled during this interval. However, once the device is online again, it will continue to send data as expected in 5-minute intervals that are consistent with the server’s clock and users will be able to remotely change their dormitory conditions through the app. Currently, the system is still in development mode, so the temperature and humidity levels are read and uploaded to the database more frequently. The 5-minute timeframe that the device is meant to operate on will be established prior to deployment.

Additionally, as previously mentioned, the device may unexpectedly shut down if the battery runs out. If the device loses power, its data syncing processthat uploads current values to the appropriate database will also be interrupted, which will result in a potentially inaccurate representation of the corresponding dormitory’s temperature and humidity conditions. Users will also find that their temperature inputs will not affect the device, as they will not be able to access the device itself because it will be powered off. The device can easily be powered by replacing its batteries, which will allow it to reconnect to BU WiFi and communicate with the server again.
Finally, the website and mobile application have simple functionalities that make it unlikely for abnormal behavior to occur.
e. | 3.1.5 | Exiting Operating Mode
The EcoSwitch device can simply be shut off by moving the “On” switch to the “Off” setting. This will shut down the ESP32 script and turn off all the individual components in the circuit as well. However, it is worth noting that the script will automatically be exited if the device runs out of power during its normal operating mode, since it relies on battery power. The batteries must remain charged in order to shut the system down properly. Additionally, if the user wants to remove the batteries in order to charge them, the device should be turned off beforehand.
There is no need to exit or shutdown the server, as it is an AWS instance that is constantly running in the background. The server is required to stay this way in order for the EcoSwitch devices to continue updating the database with their read-in values.
Similarly, the mobile application and administrator website operate independently with a permanent backend that is combined with the aforementioned AWS instance. They are both deployed through AWS every time the corresponding directory in the project’s GitHub repository is updated. Development for both applications still occur through local hosts with servers that must be manually shut down by sending a SIGINT through the terminal.

### 3.2 Operating Mode 2: Abnormal Operations

Describe any anticipated abnormal states (e.g. out-of-range data) and recovery. Have you explicitly built into the project operating modes like 'diagnostic' or 'self-test'? Describe how the project can enter and recover from such states. Is user intervention needed? Where can the users find help when a problem arises?
f. | 3.2.1 | Connection Error
1. If the EcoSwitch cannot connect to the WiFi network, restart the device and try again.
a. On device setup, the device will go into a boot loop if the device constantly fails connecting to the specified WiFi network. If the device fails to connect to the WiFi network after multiple attempts, the network itself could be causing the issue.
2. Depending on network conditions, the EcoSwitch may not be able to connect to the internet to upload sensor data or retrieve the user’s target temperature. Restarting the device can fix this issue. The device can operate without a connection; however, functionality will be extremely limited. Users will not be able to control the device from the mobile application while the device
| is offline.
3. If the user cannot connect to the EcoSwitch interface via the EcoSwitch WiFi network:
a. Try refreshing the page to see if the interface will load. If this does not work, reconnect to the EcoSwitch WiFi network and then have the page reload.
g. | 3.2.2 | Temperature Change

1. If the device is not regulating the temperature to the target temperature:
a. It could be an issue with the WiFi network and either the connection between the mobile app or the device itself. Try restarting the device or reconnecting to the WiFi network on your mobile device.
b. The target temperature may be outside the acceptable temperature range that has been set for the room. In this case, adjust the temperature you have attempted to input to one that falls within a normal range.
c. The device may not be powered due to the device being turned off or the batteries being drained. If so, turn on the device or replace the batteries.
d. The device may be locked by an administrator. If so, contact your administrator to unlock the device.
h. | 3.2.3 | Power Failure
1. If the EcoSwitch suddenly loses power due to depleted batteries, replace the batteries and turn on the device. Normal operation should resume after the booting process is finished.

### 3.3 Safety Issues

4. The EcoSwitch device uses a lithium battery pack. Users are advised to avoid putting the battery pack or the device near fire or expose it to sunlight for a long time.
5. Users are also advised to be careful not to spill liquids near the device. Spilling liquids on the top of the EcoSwitch devices may damage the electronics in the circuit board, such as the temperature sensor or microcontroller. Consequently, please do not put the device near or in wet
| areas.
6. Users should also take care of the device when the driver is in an abnormal or error status, which will cause the motor to fail to operate normally. If that occurs, students should contact the facility workers or housing administrators to follow the provided solutions above for maintenance.

### 4 Technical Background

This section includes the technical description of the EcoSwitch system and a detailed description of the interactivity between different components of the EcoSwitch system.
a. | 4.1 | Hardware Component
The EcoSwitch device uses an ESP32 microcontroller and a DHT22 sensor to fulfill its hardware functionalities. An ESP32 is ideal because it supports both WiFi and Bluetooth, which was necessary to carry out our system design. Additionally, the size of the ESP32 was suitable for the sizing limitations we were given.
The main programming language used to program the EcoSwitch device was C/C++. This allowed for control of the sensor and motor, as well as to connect to the internet. The device also uses a 3D-printed attachment, which was designed to fit onto a dial so that the device may turn the dial efficiently. The DHT22 sensor is used to accurately detect the current temperature and relative humidity of the surrounding area. An insulation material will surround the sensor and other electronics, ensuring these sensor readings are accurate.
The dial on the heating unit is moved with a stepper motor. This motor is housed in a 3D-printed shell to protect the component. Additionally, it is controlled by a L298N motor driver, which is powered by a 12V power source using 8 AA batteries. The circuit includes a 5V voltage regulator as the ESP32 pushes at most a 5V signal. The circuit also consists of both a ceramic and electrolytic capacitor in order to minimize capacitor impedance across frequencies.
The ESP32 is connected to an LCD display which will provide user feedback on the current operation of the EcoSwitch. This feedback will include current temperature and humidity levels of the room, as well as other feedback regarding device setup.
b. | 4.2 | Software Component
The EcoSwitch operates with three core software components: frontend, backend, and API. The frontend is split into two instances: one is a website for administrators to monitor the EcoSwitch devices and another is a mobile application for students to interact with their specific devices. Both frontend components are developed in React, with React JS used for the website and React Native for the mobile app. The mobile application also uses Expo to build the application onto different platforms. The backend was written in PHP and runs on an EC2 instance on AWS (Amazon Web Services).
API requests are facilitated by the use of an HTTP or HTTPS connection to the EC2 instance on AWS. The HTTP/HTTPS request supports a TCP connection. This makes the transference of data using this connection more secure and reliable. For a POST request made using an API call, once the necessary data is retrieved from the request, the backend will parse the data, convert the data into an acceptable data type, and then update the appropriate entries in the MySQL database. For a GET request, the backend will search the MySQL database for the requested record based on the parameters passed to the API. If a record is found, the record is passed back to the requester in a JSON format. If there are any errors searching for data in the database, an error is returned to the user.
The EcoSwitch API is the primary tool that allows for communication between the ESP32, mobile application, administration website, and backend. The main purpose of this API is to facilitate the movement of data between the source and destination. The interaction between these components are:
1. The EcoSwitch device sends sensor data to the MySQL database via a POST request using the API.
2. Both the mobile application and administrator website display the data via a GET request using the API.
a. The mobile application provides the most recent conditions of the room while the admin website presents the same information for all the EcoSwitch devices registered at the time.
3. The mobile application sends target temperatures to the MySQL database via a POST request.
4. The EcoSwitch device retrieves these target temperatures via a GET request from the database.
5. The EcoSwitch device calculates how far to turn the dial based on the target temperature, current temperature, and the current rate the temperature is changing in the room.
a. Based on the current rate of change, the ESP32 will “predict” if the target temperature will be achieved in 10 minutes. If the temperature will not be achieved, the device will move the heater to a more extreme setting; otherwise, the setting will remain the same.
b. This algorithm initiates automatically over a set interval.
Other functionalities that both frontend components share include a method to change the displayed temperatures between Celcius and Fahrenheit and an authentication feature for users to log into their accounts to control the EcoSwitch devices. The administrator website also has additional functionalities not previously mentioned. This section of the frontend can make a POST request using the EcoSwitch API to add authorized students to the system as well by adding new entries to the appropriate tables in the MySQL database.

### 5 Relevant Engineering Standards

IEEE 802.11 – Wireless Local and Metropolitan Area Networks:
This is a standard for frame-based data networks such as local area networks. The IEEE 802 architecture also includes a specification for the identification of public, private, and standard protocols. It relates to our project because BU WiFi is a LAN network and is used to connect the device, mobile app, and website.
IEEE 1 – General Principles for Temperature Limits in the Rating of Electrical Equipment and for the Evaluation of Electrical Insulation:
This standard includes all temperature indexes for materials and temperature classes for insulation systems. It relates to our project as temperature is an important factor to consider when choosing materials.
IEEE 1B – Guiding Principles for the Specification of Service Conditions in Electrical Standards This standard focuses on the different situations regarding usual service conditions. It applies to our project because it is expected that the device will need to be serviced by maintenance regularly. IEEE 830 – Recommended Practice for Software Requirements Specifications
This standard describes the content and qualities of a good software requirements specification. It is aimed at defining requirements of software to be developed but also aids in the selection of software products. It relates to our project as relevant software products had to be decided on.
IEEE 270 – Standard Definitions for Selected Quantities, Unites, and Related Terms, with Special Attention to the International System of Units
This standard includes definitions for physical quantities, units commonly used in technology, and related terms that concern systems of measurement. It relates to our project due to the SI units often used to describe quantities in our project.
IEEE 82079 – Standard for Preparation of Information for Use of Products
This standard gives principles and general requirements for conveying applicable information to users. Information for use is for anyone who encounters a product for the first time. It relates to our product as it is important for us to accurately describe installation and set up of the device.

### 6 Cost Breakdown

Project Costs for Production of Beta Version (Next Unit after Prototype)

Item | Quantity | Description | Unit Cost | Extended Cost
1 | 1 | ESP-WROOM-32 ESP32 ESP-32S Development Board | $10.99 | ~
2 | 1 | DHT22 Temperature Humidity Sensor | $9.95 | ~
3 | 1 | 12V battery pack | $8.00 | ~
4 | 1 | Nema 17 Stepper Motor Bipolar 2A 59Ncm | $13.99 | ~
5 | 1 | L298N Motor Drive Controller Board DC Dual H-Bridge Robot Stepper Motor Control | $6.99 | ~
6 | 1 | CopperTop AA Alkaline Batteries (8-ct) | $7.99 | ~
7 | 1 | GeeekPi 2-Pack I2C 1602 LCD Display Module | $10.99 | ~
8 | 1 | Thin Neoprene Rubber Strip 1/16 | $12.59 | ~
9 | 1 | Black Aluminum Heatsink for TO-220 Transistor | $8.99 | ~
Beta Version – Total Cost | | | | $90.48

The main constraint of this project was constructing a device as low-cost as possible to compete against currently available alternatives on the market. The biggest budget concern was the motor choice as it was the most expensive component and required some replacing throughout testing. Despite this, more than half of the budget remains.

### 7 Appendices

The EcoSwitch system’s specifications will be presented in this section, as well as the academic achievements and professional plans of the individuals that are responsible for its creation.

### 7.1 Appendix A – Specifications

Requirements | Value, Range, Tolerance, and Units
Case/Device | • Dimensions: 55mm x 55mm x 170mm • Safe to mount and tamper-proof
Power Supply | • 12V lithium battery pack • 5V and 160-260 mA in active mode for the ESP32 • 12V and 11.5 W for the stepper motor driver
Attachment Size | • Diameter: 34 mm • Height: 48.5 mm • Securely mounted on the knob of the FCU dial
Actuator | • Nema 17 Bipolar 59 Ncm (84 oz.in) 2A 42x48 mm 4 Wires w/ 1 m Cable & Connector: • The actuator is programmed to turn the FCU dial to a specific angle to switch the mode of FCU • The actuator is able to turn the dial forward and backward
Space of Server | • CPU (2.5 GHz), 1 GiB of Memory, and 8 GB SSD storage • OS: Amazon Linux 2 (Kernel 5.10)
User Interaction | • The app periodically fetches from the server every 5 minutes • The app is in cross platform
Sensor | • DHT22 Temperature Humidity Sensor • The sensor collects data every 5 minutes

Microprocessor | • ESP-WROOM-32 • Operates with the temperature sensor and sends data to the server every 5 minutes

c.

### 7.2 Appendix B – Team Information

Keven DeOliveira | Keven DeOliveira will be graduating with a bachelor’s degree in computer engineering and will then go on to work as a software engineer at Hewlett Packard Enterprise.
Samarah Uriarte | In addition to her computer engineering major, Samarah Uriarte has a concentration in Machine Learning and will be interning at Red Hat following graduation.
Michael Harkess | Michael Harkess will go on to graduate school to receive a master’s degree in Computer Engineering after graduating with a bachelor’s degree in the same field.
Michelle Thevenin | Michelle Thevenin will be working as a process integration engineer for Raytheon Missiles and Defense after graduating with a bachelor’s degree in electrical engineering.
Jiawei Liao | After graduating with a bachelor’s degree in electrical engineering, Jiawei Liao will be working as a system engineer for MBTA.

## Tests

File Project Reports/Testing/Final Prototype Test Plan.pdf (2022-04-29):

# Memo

To: | Alan Pisano

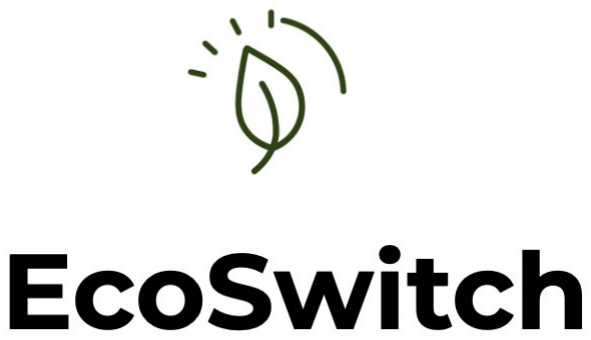
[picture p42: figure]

From: | Michelle Thevenin, Jiawei Liao, Keven DeOliveira, Samarah Uriarte, Michael Harkess
Team: 31 - EcoSwitch
Date: 4/1/22
Subject: Final Prototype Testing

### 1.0 Required Materials

Hardware:
- Microcontroller: ESP32-WROOM-32
- A computer (to show server data)
- DHT22 Temperature and Humidity Sensor
- 12V 1.5A Stepper Motor
- 12V Battery Pack
- L7805 5V Voltage Regulator
- L298N Motor Driver
- 3D printed casing
- 3D printed attachment

Software:
- Mobile application: React Native, Node.js
- Website: ReactJS, Node.js
- Server: Amazon EC2 running Linux (Debian) and Apache 2.4.51
- Database: Amazon RDS (MySQL, MariaDB)
- Arduino IDE

### 2.0 Setup

The setup is divided into hardware and software: the hardware consists of the ESP32 microcontroller, the DHT22 temperature and humidity sensor, the L298N Motor driver, a 12V stepper motor. The software consists of the mobile app, website, and server and database.
The DHT22 sensor detects the room temperature and humidity levels and sends signals to the ESP32 via pin D13 (GPIO 13). The ESP32 program then sends this data to the server that is running on a local computer. Upon reaching the server, the data is recorded in Amazon RDS (in a MySQL database) and the mobile app then queries for this data on a local phone to display the values through the interface. The website also does this, along with displaying additional test devices and their corresponding data, and it offers a registration functionality that adds and removes student information to and

# enior Design

## ENG EC 463

from a device user database when entered by the user as well. Additionally, the website provides an interface for turning off all the devices in one location. When the temperature read from the sensor is out of range with the temperature input from the mobile app, the motor will slightly turn, which would allow it to switch an FCU dial in practice.

### 2.1 Pre-Testing Setup Procedure

Server:
1. Log into AWS Console.
2. Navigate to the RDS Console and ensure MySQL database instance is running.
3. Navigate to EC2 Console and ensure the (Apache) server instance is running.

Mobile app:
1. Launch application using Expo (expo start).
2. Open application on mobile device (or laptop if WiFi is unreliable).
3. Proceed to the main page.

Website:
1. Launch project using npm (npm start).
2. Navigate website to use the available functionalities.

ESP32:
1. Ensure the ESP32 is fully connected to the computer.
2. Open the Arduino IDE and navigate to the appropriate directory.
3. Upload and run the script DHT22_with_L298N_driver_test_circuit.ino.

Hardware:
1. Attach the motor to the 3d printed attachment and put it inside the casing.
2. Add rubber strips around the FCU switch and align the attachment to the switch.
3. Align and attach the casing to the FCU with the screws on the side.

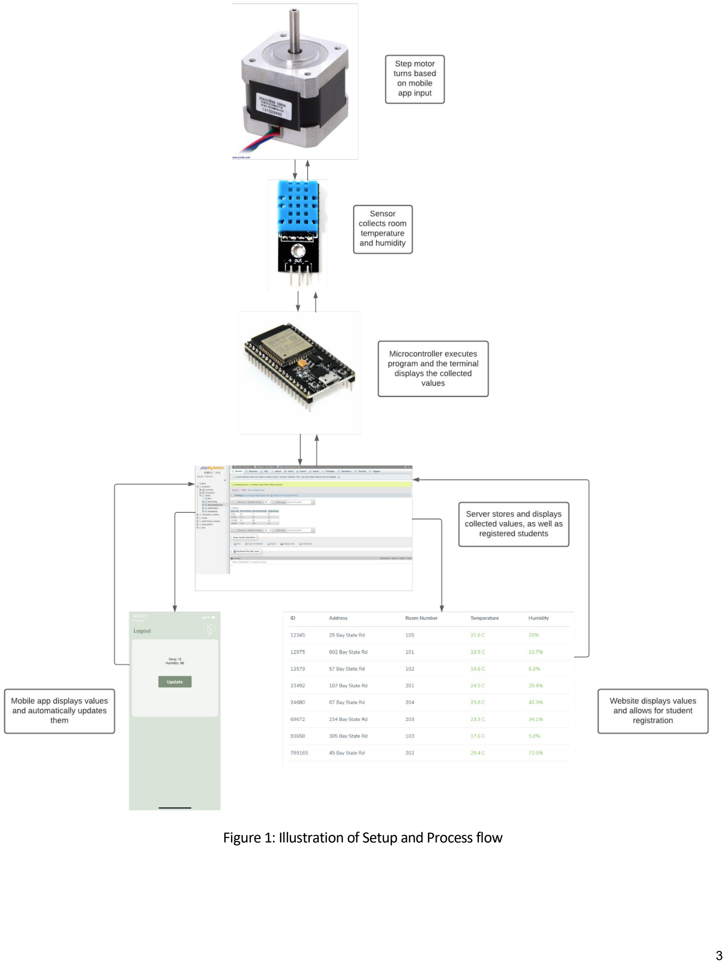
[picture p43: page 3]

Figure 1: Illustration of Setup and Process flow

### 2.2 Testing Procedure

1. Flash and monitor the ESP32 program.
2. Observe the terminal output consisting of room temperatures and humidity values.
3. Observe the room temperatures and humidity values displayed in the database.
4. Observe the room temperature and humidity value displayed in the mobile app.
5. Observe the room temperatures and humidity values displayed in the website.
6. Ensure the appropriate values match.
7. Register a test student using the website’s “Add a Student” feature.
8. Observe the test student information in the database and ensure it matches what was entered in Step 7.
9. Remove a test student using the website’s “Remove a Student” feature.
10. Observe that the test student from step 9 was removed from the database correctly.
11. Turn off all the devices in a single location using the website’s “Device Adjustment” page.
12. Observe the state in the database for the location entered in step 11 and ensure it is “0”.
13. Adjust the device temperature using the mobile application.
14. Observe the corresponding device information in the database and ensure it matches what was entered in Step 9.

### 2.3 Measurable Criteria

The criteria for successful running and output is as follows:

I. The mobile application successfully displays desired temperatures from the database.
II. | The website successfully displays data from multiple devices.
III. | The website successfully sends test student information from the correct database.
IV. | The website successfully removes test student information from the correct database.
V. The website successfully changes the state of a user-entered location to “0”, or OFF.
VI. | The server successfully receives data from the mobile device.
VII. | The values are stored in the database when received from the ESP32.
VIII. | The ESP32 successfully retrieves the desired temperature data from the server.
IX. | The ESP32 shows that the temperature was received and that the data matches what was sent.
X. The actuator operates accordingly.

### 3.0 Score Sheet

Action | Successful? (Y/N)

Did the mobile app successfully display the data read from the device?

Did the server successfully receive data when sent from the mobile app?

Are the data values stored in the database?
Is the ESP32 receiving the input temperature data from the server?

Did the motor turn based on the input temperature?
Did the website successfully display the data read from the device, as well as the hardcoded data used for testing?

Did the website successfully add a test student to the corresponding database?

Did the website successfully remove a test student from the corresponding database?

Did the website successfully turn off the devices registered under one location by setting their states to “0”?

### 4.0 Hardware Pinout

ESP32 Pin # | Usage/Description
VIN | 5V voltage supply->L298N Vcc, DHT22 Vcc, Vout of voltage regulator
GND | Ground->L298N GND, GND of voltage regulator, DHT22, two capacitors
27 | Data transmit->L298N In1
26 | Data transmit->L298N In2
25 | Data transmit->L298N In3
33 | Data transmit->L298N In4
13 | Data transmit->DHT22 data pin

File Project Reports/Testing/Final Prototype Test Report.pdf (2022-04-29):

Final Prototype Test Report Team: 31
Members: Michelle Thevenin, Jiawei Liao, Keven DeOliveira, Samarah Uriarte, Michael Harkess Test Date: 4/21/22

Equipment Summary
Hardware:
- Microcontroller: ESP32-WROOM-32
- A computer (to show server data)
- DHT22 Temperature and Humidity Sensor
- 12V 1.5A Stepper Motor
- 12V Battery Pack
- L7805 5V Voltage Regulator
- L298N Motor Driver
- 3D printed casing
- 3D printed attachment
- Lutron FSQ-2FH-DK Electronics Rotary Fan-Speed Control
- A blow dryer
Software:
- Mobile application: React Native, Node.js
- Website: ReactJS, Node.js
- Server: Amazon EC2 running Linux (Debian) and Apache 2.4.51
- Database: Amazon RDS (MySQL, MariaDB)
- Arduino IDE

Setup Summary
The setup is divided into hardware and software: the hardware consists of the ESP32 microcontroller, the DHT22 temperature and humidity sensor, the L298N Motor driver, a 12V stepper motor and a rotary Fan Speed Control. The software consists of the mobile app, website, and server and database.
The DHT22 sensor detects the room temperature and humidity levels and sends signals to the ESP32 via pin D13 (GPIO 13). The ESP32 program then sends this data to the server that is running on a local computer. Upon reaching the server, the data is recorded in Amazon RDS (in a MySQL database) and the mobile app then queries for this data on a local phone to display the values through the interface. The website also does this, along with displaying additional test devices and their corresponding data, and it offers a registration functionality that adds and removes student information to and from a device user database when entered by the user as well. Additionally, the website provides an interface for turning off all the devices in one location. When the temperature read from the sensor is out of range with the temperature input from the mobile app, the motor will slightly turn, which would allow it to switch a Fan Speed Control dial in practice. The Fan Speed Control dial goes from off, high, medium and low in clockwise direction.

Testing Summary
We first set up the testing environment which included our hardware circuit connected to a motor, attachment, and ceiling fan switch. We then explained that the DHT sensor would read in temperature and humidity information, send it to the AWS server instance we have constantly running, and store it in the database that is accessible to the mobile app and website via API calls.
Following this high-level overview of the system, we demonstrated the mobile app interface and functionalities of retrieving data from the EcoSwitch device and sending back a user-inputted temperature to the database, which then stored this value. The website was also shown, as well as the various pages that were currently available with this version. All available EcoSwitch devices and their corresponding information were queried and displayed in a clean chart. This demonstrated the website’s ability to connect to the server with the aforementioned API interface. The website was able to update the student user database by registering a student to a specific test device, as well as lock all the devices in a specific location.
To demonstrate our complete system, we input a low temperature into the app, and waited for the motor to turn our switch on. At first, our battery was not fully connected to the circuit, so the switch was not turning. Once we fixed the ground wire, the motor moved successfully with a few undesirable patterns. At the end of the testing session, all aspects were able to connect, allowing us to demonstrate the device’s functionality. While the testing process did not go completely smoothly, we were successfully able to demonstrate our device’s logic. The logic of the device is an algorithm that makes a linear approximation of the rate the temperature is changing in the room given two temperatures a set time apart. With that approximation, the algorithm predicts the future temperature of the room. If that predicted temperature is higher than the desired temperature and the current temperature is lower than the desired temperature, the algorithm will move the dial to a higher setting. This was demonstrated by heating the temperature sensor in the device and setting a high desired temperature. The algorithm moved the dial 3 places to the left (from off to low) and then moved to the right twice (from low to medium and medium to high) to get the highest setting to make the current temperature the same as the desired temperature.

Detailed Measurements

Most of the measurements made for testing were to ensure that the different components of the project were working properly in tandem. The first measurement made was confirming that the information polled by the DHT22 sensor and the ESP32 was being correctly sent to the database. Then, that the data was correctly fetched and displayed by the mobile application and administration website. These were all accurate.
Afterward, changes in temperature were made using a blowdryer. The new data was viewed in the database and then confirmed on the mobile application once the periodic updates were made. A desired temperature was set on the application to demonstrate the state logic that drives the switch. Using said logic, the dial was shown switching dial positions appropriately. The desired temperature was set to 30℃ while the room temperature read 25℃, and it was observed that the dial was turned from the “OFF” position, to the “HIGH” position.
The administration website’s functionalities were successfully demonstrated during the first attempt of testing; students were successfully added/removed, the secure login worked properly, and locking individual devices through the website worked as well. The administration website was not revisited during the final round of testing, so no further measurements were made with it at that time.

Conclusion
Since we had a total of 3 testing sessions for the final prototype testing period, we were able to improve and finalize our system after each session by using our testing results and the professors’ feedback.
The conclusion we arrived at after the first testing attempt was that, since the device was unable to turn the actual FCU switch, we should focus on finding a switch with less torque but with similar qualities to those of the FCUs. Specifically, the professors suggested that we find a switch with 4 states (“OFF”, “HIGH”, “MEDIUM”, “LOW”) and a comparable shape to the FCU switch. In addition, we were told to focus on developing the logic behind how the device interacts with the dial based on user input. Both the website and mobile applications were working as intended but were missing their login features, so this was also completed during the preparation period for the next testing session.
After the second testing session, the website and mobile applications were completed and the logic behind the device’s behavior was further advanced. There were still some inconsistencies in the system, however, due to the circuit’s individual components seemingly failing, despite the ESP32 script producing outputs that were in line with what was expected. As a result, we agreed that we should switch out the motor for a newer motor of the same type, as well as the batteries for the battery pack. Additionally, the dial we purchased was still too difficult to turn, so we seeked out another dial with significantly less torque. We also ordered a gear ratio component that we mounted on the motor.
Finally, we observed several technical issues during the third testing session that we quickly resolved upon working on the system more afterwards. Prior to this attempt, we ran through our test plan and were able to complete it and demonstrate the device’s functionality amongst ourselves. However, the wire configuration for the battery pack was damaged, leading to a lack of power in the circuit that prevented the motor from turning the dial. After testing, we concluded that we had to increase the circuit’s integrity by securing the connections between all components and replacing the batteries. Upon doing so, the device was able to turn the dial according to the input entered through the mobile app and the temperature of the surrounding air. While we were unable to test the motor with the gear ratio component during the session itself, we also examined its effectiveness at turning the more resistant fan dial and discovered that it was able to do so. As a result, we can now proceed testing on an actual FCU dial and observe the full functionality of our system in its real world application.

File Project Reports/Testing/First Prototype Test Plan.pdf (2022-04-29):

# Memo

To: | Alan Pisano


From: | Michelle Thevenin, Jiawei Liao, Keven DeOliveira, Samarah Uriarte, Michael Harkess
Team: 31 - EcoSwitch
Date: 11/16/21
Subject: First Prototype Testing

### 1.0 Required Materials

Hardware:
- Microprocessor: ESP32-WROOM-32
- A computer (to act as the power adapter and server)
- DHT11 Temperature and Humidity Sensor

Software:
- Mobile application using React Native, Node.js
- Server: XAMPP with MySQL and Apache 2.4.51
- Arduino IDE

### 2.0 Setup

The setup is divided into hardware and software: the former consists of the ESP32 microcontroller and the DHT11 temperature and humidity sensor while the latter consists of the mobile app and computer server. The DHT11 sensor detects the room temperature and humidity levels and sends 3.3 V signals to the ESP32 via pin D4 (GPIO 4). The ESP32 program then sends this data to the server that is running on the computer. Upon reaching the server, the data is stored in the MySQL database and the mobile app then queries for this data, developed with React Native on the phone to display the values on the interface.

### 2.1 Pre-Testing Setup Procedure

Server side:
1. Ensure that the server is not running.
2. Run XAMPP with admin privileges.
3. Activate Apache and MySQL.

Mobile app side:
1. Start the temporary backend service and Expo project.
a. Ensure IP address is properly configured.

# Senior Design

## ENG EC 463

2. Open the EcoSwitch app using Expo (Expo Go if on mobile) and proceed through the login page.
3. Press the “Update” button to update the temperature and humidity values with the most recent entry.
a. Alternatively, wait 30 seconds for automatic updates.

ESP32 side:
1. Ensure the ESP32 is fully connected to the computer.
2. Open the Arduino IDE and navigate to the appropriate directory.
3. Upload script.

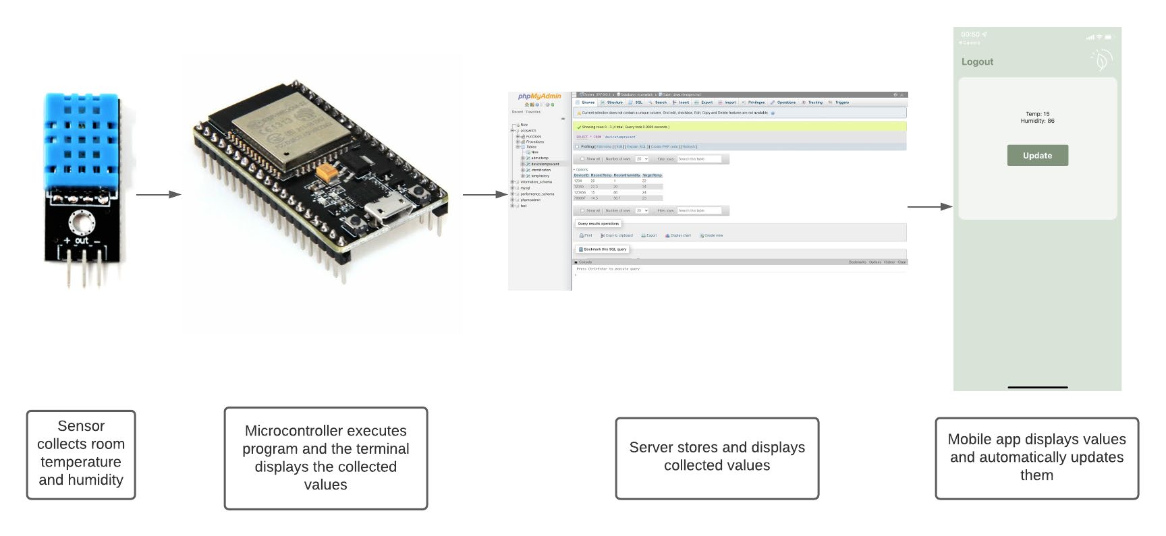
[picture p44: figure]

Figure 1: Illustration of Setup and Process flow

### 2.2 Testing Procedure

1. Flash and monitor the ESP32 program.
2. Observe the terminal output consisting of room temperatures and humidity values.
3. Observe the room temperature and humidity value displayed in the mobile app and database.
4. Ensure the values detailed in steps 2 and 3 match.
5. Ensure the room temperature and humidity values successfully update every half-minute.
a. Note: This will be changed to automatically update every minute in the final prototype.

### 2.3 Measurable Criteria

The criteria for successful running and output is as follows:

I. The microcontroller should successfully communicate with the sensor to read in accurate data. II. The server should successfully receive sensor data from the microcontroller.
III. The values should be stored in the database.

IV. The mobile app should successfully query for server data consisting of the temperature and humidity values.
V. The mobile app should successfully display these values through its interface.
VI. The displayed room temperature and humidity value should match the collected data.
VII. The room temperature and humidity values should successfully update every half-minute.
A. Note: this will be changed to every minute in the final prototype.

### 3.0 Score Sheet

Minutes Passed | ½ | 1 | 1 ½ | 2 | 2 ½ | 3

Displayed Room Temperature in Terminal (°C)

Displayed Room Humidity in Terminal (%)

Collected Room Temperature (°C)

Collected Humidity Value (%)

In the Database? (Y or N)

Same? (Y or N)

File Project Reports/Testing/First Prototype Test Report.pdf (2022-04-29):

First Prototype Test Report Team: 31
Members: Michelle Thevenin, Jiawei Liao, Keven DeOliveira, Samarah Uriarte, Michael Harkess
Test Date: 11/16/21

Equipment Summary
For the hardware aspect of our first prototype testing, we used an ESP32-WROOM-32 microcontroller, a computer that acted as the system’s power source, and a DHT11 temperature and humidity sensor. For the software side, a React Native program acted as the front end, and temporary back end, of the mobile application, XAMPP was used as the interface to the MySQL database with Apache 2.4.51, and the microcontroller was programmed in the Arduino IDE. In order to demonstrate the mobile app’s functionality, Expo Go was integrated into the testing process. Using this app, a team member connected to the EcoSwitch mobile application through a smartphone and interacted with the simple interface that was available for testing purposes. All of the equipment used during the first prototype testing was consistent with the expectations outlined in the test plan.

Setup Summary
Before testing, we set up the central server, mobile app, and ESP32 program. For the server side, we initially made sure the server was not running so the database would start collecting values once testing had begun. Then, we ran XAMPP with admin privileges and activated Apache and MySQL to run the server. For the mobile app side, we started the temporary backend service and Expo project in addition to checking that the IP address was properly configured to minimize technical errors. Following this step, we opened Expo Go on a team member’s smartphone and scanned the QR code for the EcoSwitch mobile app to access it. In order to initialize the temperature and humidity values with the most recent entry from the central server database, we pressed the “Update” button that was displayed through the mobile app’s UI. Finally, for the ESP32 side, we made certain that the device was correctly connected to a teammate’s computer. Then, we used the Arduino IDE to run the appropriate program in the corresponding directory.

Testing Summary
During testing, we first flashed and monitored the ESP32 program through the Arduino IDE and observed the terminal output consisting of the room temperature and humidity values. This data did not change until we manually refreshed the page but it was successfully queried by the mobile app client and displayed in its interface. We then compared the values in the database and the values in the app interface, ensuring that there were no discrepancies, which would have been the result of errors. Finally, we observed the time it took for the values to automatically update throughout the system, with new data values ultimately being displayed on the mobile app. As intended, it took half a minute for this to successfully occur. However, we will change this time interval to every 5 minutes in the final prototype. Figure 1 shows the workflow of our testing procedure.


Figure 1: Illustration of Setup and Process flow

Detailed Measurements
The first set of measurements taken were those of room temperature and humidity levels using the DHT11 sensor. The values themselves were generally accurate representations of the conditions of the testing room. The next “measurement” was to ensure that the values displayed on the application were the correct ones from the sensor and the database. Following this first demonstration, the sensor was then covered using fingers to skew the measurements to show that the sensor was working correctly.

Conclusion
Due to the success of our first prototype testing, we feel confident that we will be able to complete our current goals for the rest of our semester. This includes setting up a simple version of the administrator website, while ensuring it is able to query for information from the central server, and adding the actuator to the circuit, along with code to program it. Additionally, we plan to add a functionality to the app that allows it to send information back to the server, namely, temperature adjustments.
We will be making changes to the environment we were originally programming the ESP32 in, as a result of the conclusions we have arrived at based on the process of setting up the system for the first prototype test. Previously, we were working with the ESP-IDF, but upon encountering several difficulties, we switched to the Arduino IDE and this allowed us to finish all of our initial prototype goals on time. The stability and easy setup that the Arduino environment offers makes it a more optimal choice, given our time constraints.
Finally, we have noticed that the DHT11 sensor readings are more inaccurate than expected. We plan to reconsider our choice and possibly upgrade to the DHT22, though the cost is slightly higher than the DHT11.

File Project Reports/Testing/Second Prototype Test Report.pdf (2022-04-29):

Second Prototype Test Report Team: 31
Members: Michelle Thevenin, Jiawei Liao, Keven DeOliveira, Samarah Uriarte, Michael Harkess
Test Date: 3/1/22

Equipment Summary
For the hardware aspect of our second prototype testing, we used an ESP32-WROOM-32 microcontroller, a computer that acted as the system’s power source and showed server data, a 12 Volts and 1.5 Amperes Stepper Motor with a L298N Motor Driver, a 12V Battery Pack, a L7805 5V Voltage Regulator, and a DHT22 temperature and humidity sensor .
For the software side, a React Native program acted as the front end, and temporary back end, of the mobile application. Additionally, React JS was used with Node.js to design the website. For the server, we use Amazon EC2 running Linux (Debian) and Apache 2.4.51. In the database, Amazon RDS hosts the MySQL database, and the microcontroller was programmed in the Arduino IDE.
In order to demonstrate the mobile app’s functionality, Expo Go was integrated into the testing process. Using this app, a team member connected to the EcoSwitch mobile application through a smartphone and interacted with the simple interface that was available for testing purposes. The setup starts with a circuit that is already connected with the sensor, the microcontroller, the motor driver, the stepper motor and the powered battery pack. When the input temperature from the mobile app does not match the collected temperature value, the motor will slightly turn. All of the equipment used during the second prototype testing was consistent with the expectations outlined in the test plan.

Setup Summary
Before testing, we set up the server, database, mobile app, admin website and the ESP32 program. For the server side, we initially made sure both the server and database instances on AWS were not running so that it would start collecting values once testing had begun. Then, we initiated the server and database instances in AWS and made some test queries to ensure activation. For the mobile app side, we opened Expo Go on a team member’s smartphone and scanned the QR code for the EcoSwitch mobile app to access it. In order to initialize the temperature and humidity values with the most recent entry from the server database, we pressed the “Update” button that was displayed through the mobile app’s UI. To update the database with the user’s desired temperature we typed a value into the provided text box and submitted the response by pressing the “Set” button displayed in the app’s UI.
For the admin website, we started a Node.js instance on a team member’s computer and navigated to both the Main and StudentAdd pages. For the main page, to initialize the temp and humidity values for every unique entry in the database, we pressed the “Get Data” button displayed by the website’s UI. For the StudentAdd page, we put some test values into the displayed text boxes and pressed the “Submit” button that was displayed to update the database. Finally, for the ESP32 side, we made certain that the device was correctly connected to a teammate’s computer. Then, we used the Arduino IDE to run the appropriate program in the corresponding directory. We also made sure that the motor connected to the ESP32 had sufficient batteries to power the component as well as making sure the battery housing was providing power to the motor.

Testing Summary
We first set up the testing environment, with a few exceptions that were required to be built as we described the testing procedure and how our solution worked on a high level. The description of our second prototype included the circuit and its new additions, which consist of the step motor, the corresponding driver, the voltage regulator, and the battery pack that powered it. The other components that were present in the first prototype were the DHT sensor and the ESP32. We then explained that the DHT sensor would read in temperature and humidity information, send it to the AWS server instance we have constantly running, and store it in the database that is accessible to the mobile app and website via API calls.
Following this high-level overview of the system, we demonstrated the mobile app interface and functionalities of retrieving data from the EcoSwitch device and sending back a user-inputted temperature to the database, which then stored this value.
The website was also shown, as well as the various pages that were currently available with this version. All available EcoSwitch devices and their corresponding information were queried and displayed in a clean chart once the appropriate button was pressed. This demonstrated the website’s ability to connect to the server with the aforementioned API interface.
Unfortunately, we were facing WiFi issues that prevented the ESP32 script from connecting to BU WiFi, which impeded the program from controlling the actuator based on the user input that was retrieved from the mobile app. At the end of the testing session, the ESP32 was able to connect, allowing us to demonstrate this functionality as well, however, with a few undesirable patterns. Similarly, the website was unable to update the student user database by registering a student to a specific test device as a result of API connection difficulties. With previous testing sessions prior to the official prototype testing, the script that was responsible for this mechanism successfully established a connection with the API endpoint that represented the student user database and allowed users to add students to it without issues. While the testing process did not go completely smoothly, we were provided with a great deal of advice and have a good sense of what our next steps will be.

Detailed Measurements

Most of the measurements made for the prototype testing were ensuring that aspects of the project were working as anticipated when tested real-time. The first measurement made was confirming that the information gathered by the sensor was accurately delivered to the mobile device. We verified that the values present on the phone were the same as those logged in the ESP32 console, as well as the values stored in the database. This was similar to the first prototype testing.
Following this, we began demonstrating the new functionalities of the project. We entered a desired temperature through the mobile application and sent it, then confirmed that the database received that information correctly. We also ensured that the database successfully relayed the data to the ESP32. Once the ESP32 received the information, we were able to demonstrate that it was accurate using the console, and the motor spun. However, at the time of testing, the motor functionality was not working as fully desired; there were some bugs in the programming that were fixed afterwards.
The administrator website was able to display dummy data that was manually entered into the database, as well as the information from the ESP32 sensor used in testing. However, due to a bug in the API calls, we were unable to demonstrate and measure the success of adding a new device/student via the website.

Conclusion
Upon completion of the testing, it was determined that the holding torque of the stepper motor is ultimately not enough to turn the switch. Additionally, the motor that connects vertically to the attachment needs to be supported. To solve these testing issues, a stronger stepper motor will be bought and mounted onto the attachment. An additional piece that can be screwed onto the FCU will be implemented to apply a downward force on the motor to hold it down. This box will also serve as an insulator for the circuit so that the temperature sensor is not affected by the active FCU. There are two screw holes on the side of the FCU switch that will be used for the purpose of securing the insulation box. These two design changes will provide a direct force to eventually turn the switch under the attachment.
On the software end of the project, the app and website currently have working functionalities that need to be updated further. The mobile application needs Google authentication, UI updates, and to be tested extensively. The website also needs Google authentication along with POST request functionalities and an updated UI. Once the hardware mechanisms have been established, our final step would be to determine the logic in the device software that we will use to automatically turn the switch to reach the user desired temperature.

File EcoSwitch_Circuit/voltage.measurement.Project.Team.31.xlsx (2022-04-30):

 | Voltage(V) | Current(A) | Power(W) | total(KW/h)
From ESP:Vin and GND | 5 | 0.2 | 1 | 0.00580000144
From power supply and GND | 12 | 1.2e-07 | 1.44e-06
motor | 12 | 0.4 | 4.8

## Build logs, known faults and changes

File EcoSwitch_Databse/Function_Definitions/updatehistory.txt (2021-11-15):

DELIMITER $$
CREATE DEFINER=`admin`@`%` PROCEDURE `updateHistory`(IN `ID` INT(32), IN `newTemp` FLOAT(32), IN `newHumid` FLOAT)
BEGIN
DECLARE Thistory longtext;
DECLARE Hhistory longtext;

SELECT Temps INTO Thistory from ecoswitch.temphistory WHERE DeviceID = ID;

SELECT Humiditys INTO Hhistory from ecoswitch.temphistory WHERE DeviceID = ID;

SELECT JSON_ARRAY_INSERT(Thistory, '$[0]', newTemp);
SELECT JSON_ARRAY_INSERT(Hhistory, '$[0]', newHumid);

UPDATE ecoswitch.temphistory
SET Temps = Thistory,Humiditys = Hhistory 
WHERE DeviceID = ID;

END$$
DELIMITER ;

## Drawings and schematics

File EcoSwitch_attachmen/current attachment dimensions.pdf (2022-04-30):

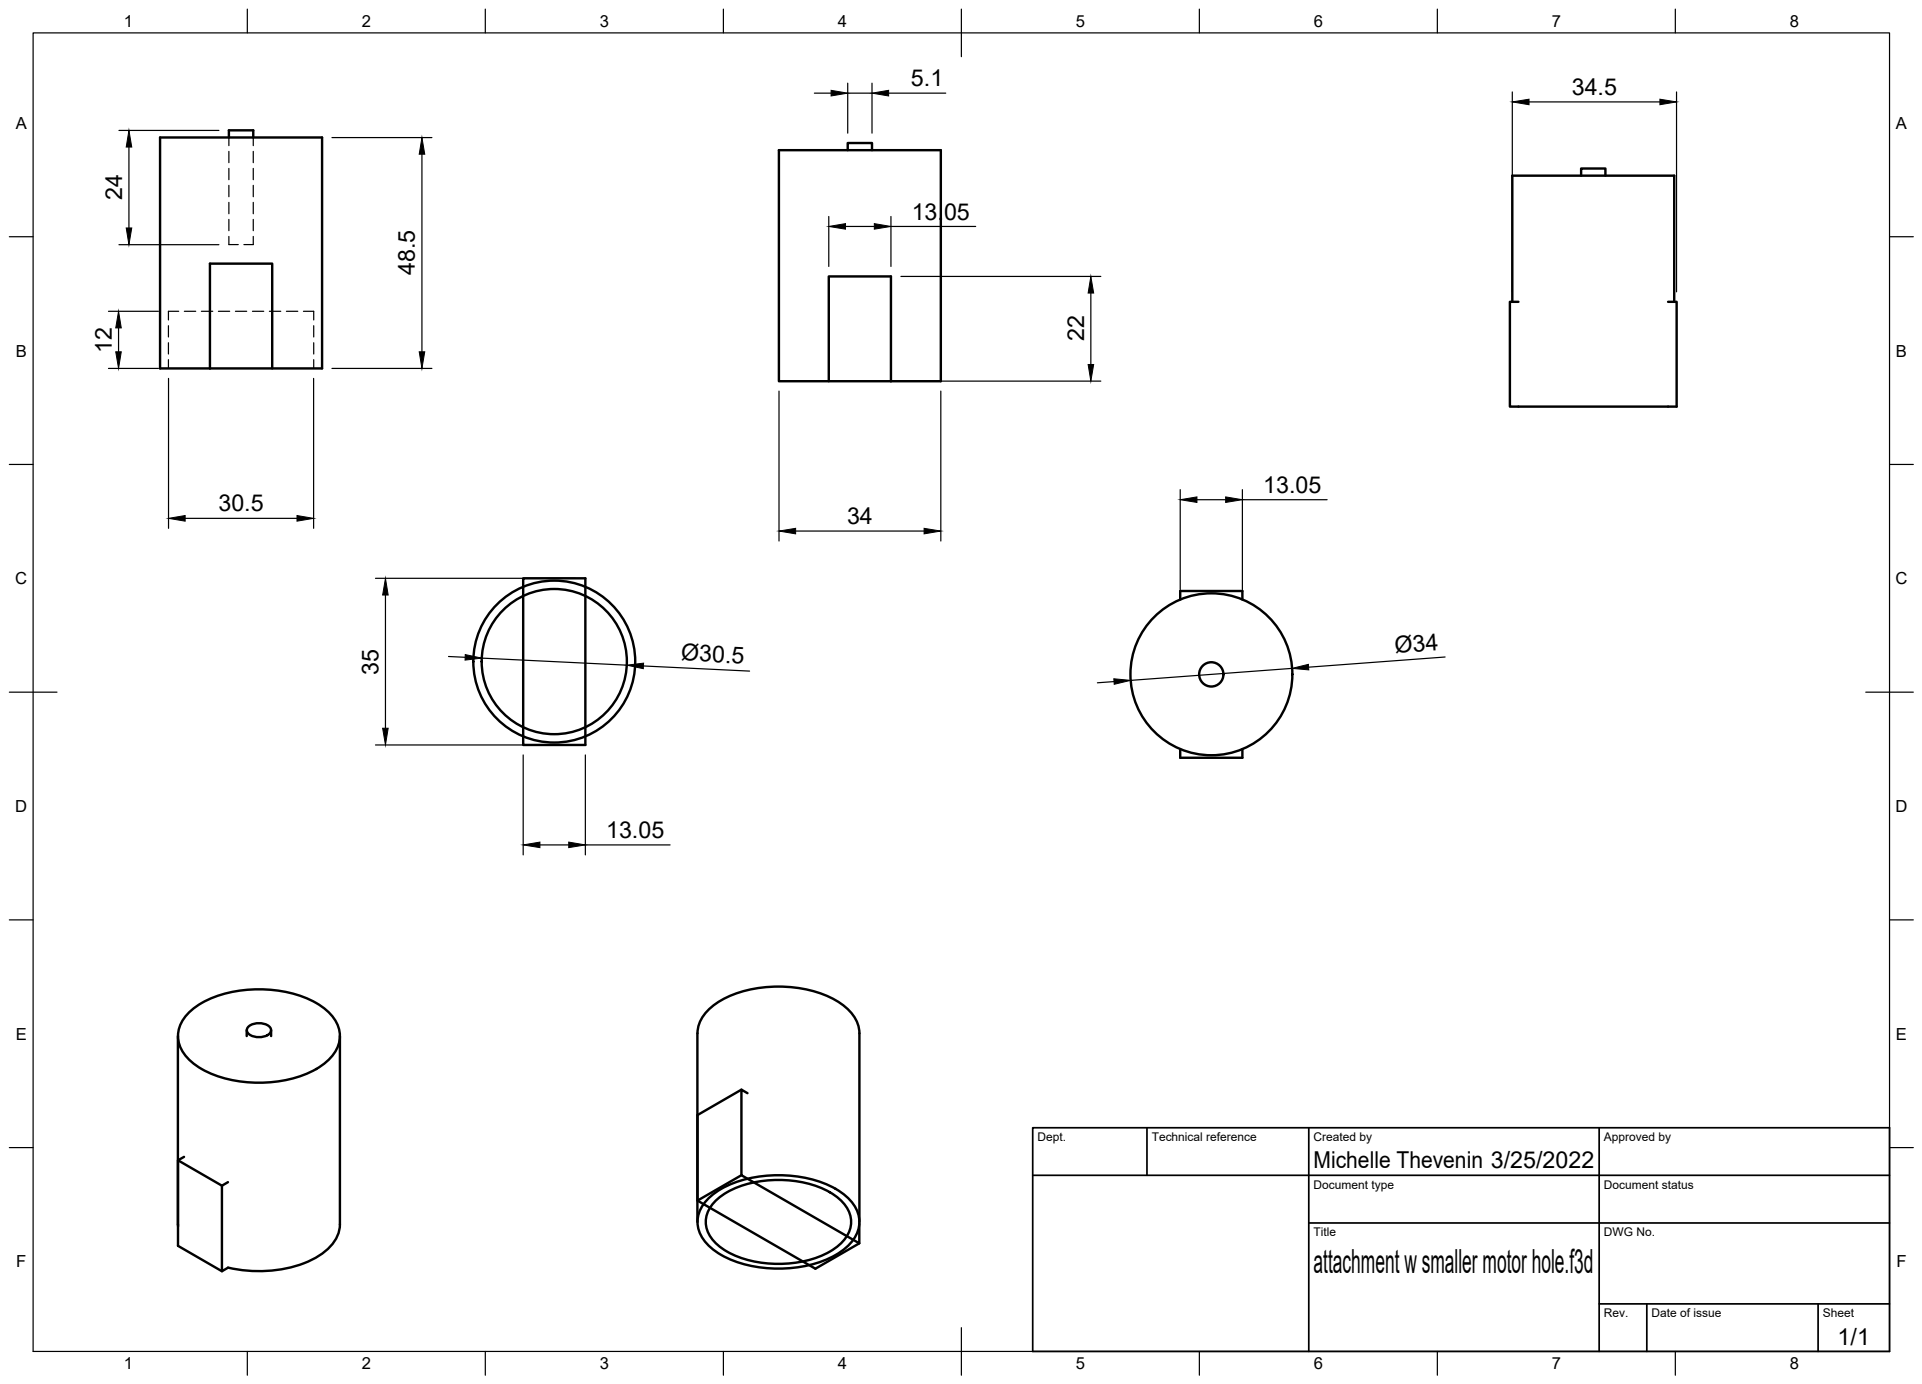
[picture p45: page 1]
Title; DWG No.; Rev.; Date of issue; Sheet

Dept. | Technical reference | Created by Michelle Thevenin 3/25/2022 | Approved by

Document type | Document status

attachment w smaller motor hole.f3d

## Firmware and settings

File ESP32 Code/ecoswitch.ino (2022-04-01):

//Library imports
#include <Arduino.h>
#include <WiFi.h>
#include <string>
#include "esp_wpa2.h" //wpa2 library for connections to Enterprise networks
#include <HTTPClient.h>
#include "DHT.h"
#include <Preferences.h>
#include <stdio.h>
#include <Stepper.h>
#include <WebServer.h>

//DHT sensor
uint8_t DHTPin = 13;
#define DHTTYPE DHT22

//Declaration of global variables
#define USE_SERIAL Serial
int counter = 0;
String ID = "12345"; //Device ID number
float target_temp = 23;   //Target temperature for heating, in Celcius
int wifi_success = 2;
Preferences saved_data;

char* webssid = "EcoSwitch";
char* webpassword = "12345678";
IPAddress local_ip(192,168,1,1);
IPAddress gateway(192,168,1,1);
IPAddress subnet(255,255,255,0);
WebServer webserver(80);
String winame;
String pass;
String user;
bool continueSetup = false;

//Initialization for DHT sensor
DHT dht(DHTPin, DHTTYPE);

const int stepsPerRevolution = 200;

// Motor Driver Pins
#define IN1 27
#define IN2 26
#define IN3 25
#define IN4 33
#define DCMOTORDRIVERL298_PIN_ENA  32
// initialize the stepper library
Stepper myStepper(stepsPerRevolution, IN1, IN3, IN2, IN4);

//Webserver Pages and Handlers

//---------------------------------------------------------
void handleNotFound() {
  webserver.send(404, "text/plain", "Page not found ...");
}

//---------------------------------------------------------
void handleSave() {
  String str = "Settings Saved ... Now Connecting to Wifi...\r\n";
 
  if (webserver.args() > 0 ) {
      winame = webserver.arg(0);
      pass = webserver.arg(1);
      saved_data.putString("SSID", winame);
      saved_data.putString("WifiPassword", pass);
      if (webserver.args() > 1){
        user = webserver.arg(2);
        saved_data.putString("WifiUsername", user);
      }
      continueSetup = true;
  
  }
  webserver.send(200, "text/plain", str.c_str());
}
//---------------------------------------------------------
static const char PROGMEM EXAMPLE_HTML[] = R"rawliteral(
<!DOCTYPE html>
<html>
    <head>
        <meta name="viewport" content="width=device-width, initial-scale=1">
        <style>
            body {
                color: #434343;
                font-family: "Helvetica Neue",Helvetica,Arial,sans-serif;
                font-size: 14px;
                line-height: 1.42857142857143;
                padding: 20px;
            }

            .container {
                margin: 0 auto;
                max-width: 400px;
            }

            form .field-group {
                box-sizing: border-box;
                clear: both;
                padding: 4px 0;
                position: relative;
                margin: 1px 0;
                width: 100%;
            }

            form .field-group > label {
                color: #757575;
                display: block;
                margin: 0 0 5px 0;
                padding: 5px 0 0;
                position: relative;
                word-wrap: break-word;
            }

            input[type=text] {
                background: #fff;
                border: 1px solid #d0d0d0;
                border-radius: 2px;
                box-sizing: border-box;
                color: #434343;
                font-family: inherit;
                font-size: inherit;
                height: 2.14285714em;
                line-height: 1.4285714285714;
                padding: 4px 5px;
                margin: 0;
                width: 100%;
            }

            input[type=text]:focus {
                border-color: #4C669F;
                outline: 0;
            }

            .button-container {
                box-sizing: border-box;
                clear: both;
                margin: 1px 0 0;
                padding: 4px 0;
                position: relative;
                width: 100%;
            }

            button[type=submit] {
                box-sizing: border-box;
                background: #f5f5f5;
                border: 1px solid #bdbdbd;
                border-radius: 2px;
                color: #434343;
                cursor: pointer;
                display: inline-block;
                font-family: inherit;
                font-size: 14px;
                font-variant: normal;
                font-weight: 400;
                height: 2.14285714em;
                line-height: 1.42857143;
                margin: 0;
                padding: 4px 10px;
                text-decoration: none;
                vertical-align: baseline;
                white-space: nowrap;
            }
        </style>
    </head>
    <body>
        <div class="container">
            <h1 style="text-align: center;">EcoSwitch Wifi Details</h1>
            <form method="post" action="/save">
                <div class="field-group">
                    <label>SSID</label>
                    <input name="ssid" type="text" length=32>
                </div>
                <div class="field-group">
                    <label>Password</label>
                    <input name="password" type="text" length=64>
                </div>
                <div class="button-container">
                    <button type="submit">Save</button
                </div>
            </form>
              <form action="/enterprise">
             <div class="button-container">
                    <button type="submit">Go To Enterprise Setup</button
                </div>
                </form>
        </div>
    </body>
</html>
)rawliteral";

//---------------------------------------------------------
void handleExample() {
  webserver.send(200, "text/html", EXAMPLE_HTML);
}

//---------------------------------------------------------
static const char PROGMEM ENTERPRISE_HTML[] = R"rawliteral(
<!DOCTYPE html>
<html>
    <head>
        <meta name="viewport" content="width=device-width, initial-scale=1">
        <style>
            body {
                color: #434343;
                font-family: "Helvetica Neue",Helvetica,Arial,sans-serif;
                font-size: 14px;
                line-height: 1.42857142857143;
                padding: 20px;
            }

            .container {
                margin: 0 auto;
                max-width: 400px;
            }

            form .field-group {
                box-sizing: border-box;
                clear: both;
                padding: 4px 0;
                position: relative;
                margin: 1px 0;
                width: 100%;
            }

            form .field-group > label {
                color: #757575;
                display: block;
                margin: 0 0 5px 0;
                padding: 5px 0 0;
                position: relative;
                word-wrap: break-word;
            }

            input[type=text] {
                background: #fff;
                border: 1px solid #d0d0d0;
                border-radius: 2px;
                box-sizing: border-box;
                color: #434343;
                font-family: inherit;
                font-size: inherit;
                height: 2.14285714em;
                line-height: 1.4285714285714;
                padding: 4px 5px;
                margin: 0;
                width: 100%;
            }

            input[type=text]:focus {
                border-color: #4C669F;
                outline: 0;
            }

            .button-container {
                box-sizing: border-box;
                clear: both;
                margin: 1px 0 0;
                padding: 4px 0;
                position: relative;
                width: 100%;
            }

            button[type=submit] {
                box-sizing: border-box;
                background: #f5f5f5;
                border: 1px solid #bdbdbd;
                border-radius: 2px;
                color: #434343;
                cursor: pointer;
                display: inline-block;
                font-family: inherit;
                font-size: 14px;
                font-variant: normal;
                font-weight: 400;
                height: 2.14285714em;
                line-height: 1.42857143;
                margin: 0;
                padding: 4px 10px;
                text-decoration: none;
                vertical-align: baseline;
                white-space: nowrap;
            }
        </style>
    </head>
    <body>
        <div class="container">
            <h1 style="text-align: center;">EcoSwitch Enterprise Wifi Details</h1>
            <form method="post" action="/save">
                <div class="field-group">
                    <label>SSID</label>
                    <input name="ssid" type="text" length=32>
                </div>
                <div class="field-group">
                    <label>Username</label>
                    <input name="username" type="text" length=64>
                </div>
                <div class="field-group">
                    <label>Password</label>
                    <input name="password" type="text" length=64>
                </div>
                <div class="button-container">
                    <button type="submit">Save</button
                </div>
            </form>
             <form action="/">
             <div class="button-container">
                    <button type="submit">Go To Consumer Setup</button
                </div>
                </form>
        </div>
    </body>
</html>
)rawliteral";

//---------------------------------------------------------
void handleEnterprise() {
  webserver.send(200, "text/html", ENTERPRISE_HTML);
}



//---------------------------------------------------------------------------------------------------------------------------------
//Setup for wifi, only to be used once on "factory settings"
int wifi_setup(){

  delay(3000);
  String continueConnect;

  WiFi.softAP(webssid, webpassword);
  Serial.println("");
  WiFi.softAPConfig(local_ip, gateway, subnet);

  webserver.on("/", handleExample);
  webserver.on("/save", handleSave);
  webserver.onNotFound(handleNotFound);
  webserver.on("/enterprise", handleEnterprise);
  webserver.begin();
  Serial.println("Web server has started");
  while (true){
    webserver.handleClient();
    if (continueSetup){
      break;
    }
  }
  
  
    WiFi.mode(WIFI_STA); //init wifi mode
     if(saved_data.getString("WifiUsername", "") == ""){
    //INITIATE CONSUMER GRADE SETUP
    WiFi.begin(winame.c_str(), pass.c_str());
  }else{
    esp_wifi_sta_wpa2_ent_set_identity((uint8_t *)user.c_str(), strlen(user.c_str())); //provide identity
    esp_wifi_sta_wpa2_ent_set_username((uint8_t *)user.c_str(), strlen(user.c_str())); //provide username --> identity and username is same
    esp_wifi_sta_wpa2_ent_set_password((uint8_t *)pass.c_str(), strlen(pass.c_str())); //provide password
    esp_wpa2_config_t config = WPA2_CONFIG_INIT_DEFAULT();
    esp_wifi_sta_wpa2_ent_enable(&config);
    WiFi.begin(winame.c_str()); //starts process to connect to wifi
  }
  USE_SERIAL.println("Connecting...");
  while (WiFi.status() != WL_CONNECTED) { //Retry connection if failed to connect to wifi
    delay(500);
    USE_SERIAL.print(".");
    counter++;
    if(counter>=60){ //after 30 seconds timeout - reset board
       USE_SERIAL.println("Connection Timeout, Continue Trying? Y/N");
       while (true){
        if (USE_SERIAL.available()>0){
          continueConnect = USE_SERIAL.readString();
        }
        if (continueConnect[0] == 'N' || continueConnect[0] == 'n'){
          USE_SERIAL.println("Clearing Memory...");
          saved_data.clear();
          ESP.restart();
        }
       }
    }
  }
  USE_SERIAL.println("");
  USE_SERIAL.println("WiFi connected");
  USE_SERIAL.println("IP address set: "); 
  USE_SERIAL.println(WiFi.localIP()); //print LAN IP

  return 0;
    
}

void wifi_quickstart(){ //skips setup process and connects to wifi with saved data
  
  //Lets the user reset device to original state
  delay(3000);
  USE_SERIAL.println("Would you like a factory reset? Y/N");
  String fr;
  while (true){
      if (USE_SERIAL.available() > 0){
        fr = USE_SERIAL.readStringUntil('\n');
      }
      if (fr[0] == 'y' || fr[0] == 'Y'){
        factory_reset();
      }
      if (fr[0] == 'n' || fr[0] == 'N'){
        break;
      }
    }

    //Setup for wifi
  USE_SERIAL.println("Wifi Quickstart Setup...");
  String ssid;
  String password;
  ssid = saved_data.getString("SSID");
  password = saved_data.getString("WifiPassword");
  
  if(saved_data.getString("WifiUsername", "") == ""){
    //INITIATE CONSUMER GRADE SETUP
    USE_SERIAL.println("Consumer Wifi Quickstart...");
    WiFi.begin(ssid.c_str(),password.c_str());
  }
  else{
    WiFi.mode(WIFI_STA); //init wifi mode
    USE_SERIAL.println("Enterprise Wifi Quickstart...");
    String username = saved_data.getString("WifiUsername");
    esp_wifi_sta_wpa2_ent_set_identity((uint8_t *)username.c_str(), strlen(username.c_str())); //provide identity
    esp_wifi_sta_wpa2_ent_set_username((uint8_t *)username.c_str(), strlen(username.c_str())); //provide username --> identity and username is same
    esp_wifi_sta_wpa2_ent_set_password((uint8_t *)password.c_str(), strlen(password.c_str())); //provide password
    esp_wpa2_config_t config = WPA2_CONFIG_INIT_DEFAULT();
    esp_wifi_sta_wpa2_ent_enable(&config);
    WiFi.begin(ssid.c_str()); //starts process to connect to wifi
  }
  while (WiFi.status() != WL_CONNECTED) { //Retry connection if failed to connect to wifi
    delay(500);
    USE_SERIAL.print(".");
    counter++;
    if(counter>=60){ //after 30 seconds timeout - reset board
      ESP.restart();
    }
  }
  USE_SERIAL.println("");
  USE_SERIAL.println("WiFi connected");
  USE_SERIAL.println("IP address set: "); 
  USE_SERIAL.println(WiFi.localIP()); //print LAN IP

}


void factory_reset(){ //clears all saved data and restarts ESP32
  USE_SERIAL.print("Factory Reset Initiated...");
  saved_data.clear();
  ESP.restart();
}


void setup() {
  USE_SERIAL.begin(115200);
  // set the speed at 5 rpm
  myStepper.setSpeed(stepsPerRevolution);
  delay(10);
  //intiates process to save important data to flash memory
  saved_data.begin("Ecoswitch_data",false);
  
  dht.begin();
}


void loop() {
                                                                                                                                           
         
         //Wifi Setup (doesn't work in setup() function, so must be added here
         while (wifi_success > 1){
          if (saved_data.getString("SSID", "NA") == "NA"){
           wifi_success = wifi_setup();
           }
          else{
            wifi_quickstart();
            wifi_success = 0;
   }
  }
         // Reading temperature or humidity takes about 250 milliseconds!
        // Sensor readings may also be up to 2 seconds 'old' (its a very slow sensor)
        float h = dht.readHumidity();
        // Read temperature as Celsius (the default)
        float t = dht.readTemperature();
          // Check if any reads failed and exit early (to try again).
        if (isnan(h) || isnan(t)) {
          Serial.println(F("Failed to read from DHT sensor!"));
        }
        USE_SERIAL.print(h);
        USE_SERIAL.print("\n");
        USE_SERIAL.print(t);
        USE_SERIAL.print("\n");
        //int wifi_success;
        //wifi_success = wifi_setup();
        
        HTTPClient https;

        USE_SERIAL.print("[HTTPS] begin...\n");
        // configure targeted server and url
        //URL Arguments for targeted PHP page
        String arguments = "?temperature=" + String(t) + "&humidity=" + String(h) + "&deviceID=" + String(ID);
        //Connects to targeted page
        https.begin("https://3.12.233.95/device_dataUpdate.php" + arguments); //HTTPS

        USE_SERIAL.print("[HTTP] GET...\n");
        // start connection and send HTTP header
        https.addHeader("Content-Type", "application/x-www-form-urlencoded");
        int httpCode = https.sendRequest("GET","message_sent=HELLO");

        // httpCode will be negative on error
        if(httpCode > 0) {
            // HTTP header has been send and Server response header has been handled
            USE_SERIAL.printf("[HTTP] POST... code: %d\n", httpCode);

            // file found at server
            if(httpCode == HTTP_CODE_OK) {
                String payload = https.getString(); //gets string message server sends back
                if (payload.toFloat() < 0.9*t){
                  Serial.println("clockwise");
                  myStepper.step(stepsPerRevolution);
                  delay(1000);
                }
                  if (payload.toFloat() > 1.1*t){
                  Serial.println("counterclockwise");
                  myStepper.step(-stepsPerRevolution);
                  delay(1000);
                }
                USE_SERIAL.println(payload);
            }
        } else {
            USE_SERIAL.printf("[HTTP] GET... failed, error: %s\n", https.errorToString(httpCode).c_str());

        https.end(); //ends HTTP connection
    }

    delay(6000); //Time between measurements (12 seconds)
}

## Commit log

2021-11-02 Server function test from Client-side
    -Tests using a server-side function from the client (in this case it is Celsius to Fahrenheit converter)
    -Written in Python (possibly a different language in the future)
2021-11-04 Table Update Testing
    -Code to test to see if a table in the MySQL database with update given the desired parameters
    - Specifically modifies the "TargetTemp" column of the "devicetemprecent" table given the Device ID
2021-11-08 Additional Server Function Definitions
    - Added functions with the purpose of reducing the number of calls to the server by the app or the device
    - All functions take an input of at least the DeviceID in order to index the database to find the correct data
    - Code is not an actual file, but input in MySQL terminal when running the command: 'CREATE FUNCTION' or 'CREATE PROCEDURE'
2021-11-09 Device Update Data Mechanism
    - Added a php file for the device to make a php query to update data in Database
    - redacted password for user to maintain security
    - will return different values if connection to server is established or if data is updated successfully
2021-11-12 Temp History Updates
    - Added a server function that will update the list of history temperatures and humidity's with the most recent value that was updated in the database
2021-11-15 Added code to read in sensor data
2021-11-16 fixed issue where iOS devices could not complete GET request
2021-11-16 fixed typo in display, set deviceID
2021-11-16 Reads sensor data and sends to server
2021-11-18 Arduino Device Code
    - Code made in the Arduino IDE for the device
    - Can connect to a WPA2 (Enterprise) Wifi Network
    - Can take temperature and humidity readings from a DHT11 Sensor
    - Can upload data collected to a remote server with a MySQL database via URL arguments
    - Uploads data in increments of 12 seconds (can be changed)
2022-01-25 Added new styles and function to switch temperature from F/C
2022-01-25 Added button for metric conversion, tidied up function
2022-01-25 Added temporary styles for metric button and text
2022-01-27 ESP 32 Wifi Connectivity
    - Added a process for the user to setup wifi through Serial Terminal (One-Time process)
    - Added Quick Connect feature to quickly connect to wifi with saved credentials
    - Added Factory Reset feature to wipe device memory and restart the setup process
    - Added Processes to connect to either Enterprise or Consumer level wifi
    - Added Serial Terminal prompts to guide user through set up process
    [wifi_server_connection.ino]
2022-02-07 App request API to database
    - Added API calls on EC2 as a PHP file to interact between the database and the client (mobile app and admin website)
    - Fixed CORS issue when requesting data from these webpages from the client
    - API endpoint returns a JSON datatype instead of HTML (in the basic format of: {DeviceID: ******, Temp: ***, Humidity: ***})
    - allRecent.php returns a JSON list of every device and their data to the Client (namely for admin website)
2022-02-10 added POST request and temp button for testing
2022-02-15 Database/Server Guide
    - Added a Guide for the MySQL Database/Apache server setup on AWS
    - In guide, added an API list to document the current API that are available to use on AWS
2022-02-28 ready for 2nd prototype testing
2022-02-28 added status msgs, ready for prototype demo
2022-03-01 Create wifi_motor_integration.ino
    - Integrated Wifi and Motor capabilities of ESP32
2022-03-01 Update wifi_motor_integration.ino
    - typo corrections
    [wifi_motor_integration.ino]
2022-03-01 Fixed Regular Wifi Setup
    - Changed method of reading input from consumer wifi setup
    [wifi_motor_integration.ino]
2022-03-02 Update README.md
    - Updated server domain address to reflect current address
2022-03-03 Motor Movement Enhancement
2022-04-01 Added HTML form to device setup
    - Added an HTML form to retrieve wifi credentials from user
    - Added a webserver on "First-time-setup" on Access-point mode
2022-04-01 ready for final prototype testing
2022-04-11 added commented code that can filter only bu logins
2022-04-13 Added Algorithm for ESP32
    - Added Algorithm integration to ESP32 code
    - Need to fix state change error (only changes once) and add "Locking" Mechanism
    [Ecoswitch_Algorithm.ino]
2022-04-13 Fixed Algorithm State Changes
    - changed Algorithm state changes to reflect heating positions of the dial
    - Added better UI in Serial Terminal for better readability
    - Added Locking mechanism in algorithm, still need to add API request to grab admin locking state
    [Ecoswitch_Algorithm.ino]
2022-04-13 Added Locking Mechanism API Call
    - Added an API request to retrieve admin lock state for a device
    - Algorithm will turn off FCU and "lock" the device (requests to change temperature from students will be ignored)
    - Algorithm can also "unlock" the device based on return value of API call
2022-04-15 Updated ESP code
    - Fixed Motor rotation issues (now makes smooth turns instead of stuttering)
    - Added HTML interface for UI after setup process
    - Shortened loop time for demonstration purposes
    [Ecoswitch_Algorithm.ino]
2022-04-20 Added New API Call
    - Added API call to add new devices to SQL database
2022-04-22 Fixed device registration form
2022-04-29 added flow diagram for app
2022-04-29 added flow diagram
2022-04-29 Flow chart for Backend
2022-04-29 Flow Chart Re-upload
2022-04-30 Added Images for ESP32 README
2022-04-30 Added Images to ESP32 README
2022-04-30 Create circuit_README
